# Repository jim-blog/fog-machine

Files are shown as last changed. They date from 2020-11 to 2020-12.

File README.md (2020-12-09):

# Fog Machine Control
*Control a fog machine with Arduino UNO and NW.js React app.*

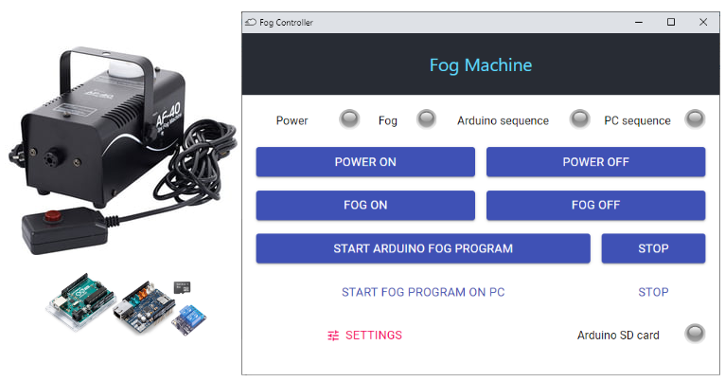
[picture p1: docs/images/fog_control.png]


## Overview

The Fog Machine is one of the most popular props in Escape Rooms, offering spooky supernatural effects or revealing light or laser beams.

## What we need

* basic fog machine with a ***wired*** remote control
* Arduino UNO with Ethernet shield and SD card
* SRD relay shield

 120/220V **10A** relays are required because fog machine power is 400W - 700W or more.</src>

## Hacking the fog machine
It is as simple as cutting and rewiring the power cable and the remote control cable.

> Open the wired remote control box and replace the pushbutton connection with a connection to the SRD relay shield.

This video may help: 
* <a href="https://www.youtube.com/watch?v=Y6d89PBlxrk" target="_blank">Controlling a Fog Machine with a Prop Controller or Relay</a>

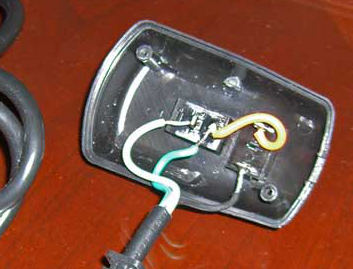
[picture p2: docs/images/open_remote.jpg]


## Wiring the Arduino prop and the fog machine
The SD card is necessary to store the fog sequence but optional if you want to control the fog sequence from the controller app only:
> Fog sequence: spit fog for *T2* seconds, pause *T3* seconds, do that *N* times then pause *T1* minutes and starts again for ever.

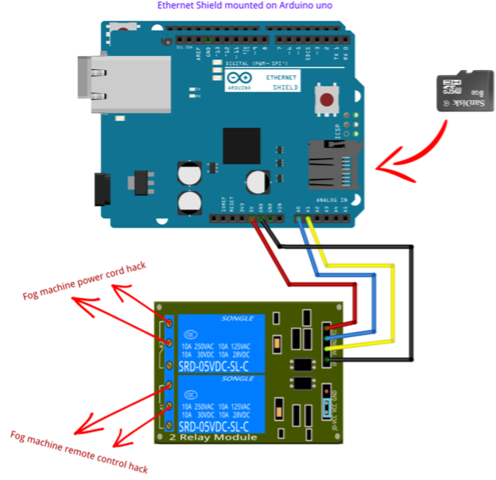
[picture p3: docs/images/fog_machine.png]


## Edit and upload the Arduino sketch

Install lastest <a href="https://www.arduino.cc/en/software" target="_blank">Arduino IDE</a> and download the <a href="https://github.com/jim-blog/fog-machine/raw/master/arduino/FogMachine.zip" target="_blank">FogMachine sketch</a> available from <a href="https://github.com/jim-blog/fog-machine/tree/master/arduino" target="_blank">this GitHub repository</a>.

Open **FogMachine** sketch in Arduino IDE and set the Arduino IP address:

```cpp
String ip = "192.168.1.201"; //<<< ENTER YOUR IP ADDRESS HERE
```

Upload **FogMachine** sketch to the Arduino

```dos
Sketch uses 27460 bytes (85%) of program storage space. Maximum is 32256 bytes.
Global variables use 1127 bytes (55%) of dynamic memory, leaving 921 bytes for local variables. Maximum is 2048 bytes.

```

## Install Fog Controller app for Windows

Download and unzip the app archive:
* <a href="https://github.com/jim-blog/fog-machine/raw/master/bin/win64/fog-controller-win64.zip">fog-controller-win64.zip</a> (92.1 MB)

Alternatively, download the `.7z` app archive and unzip with <a href="https://www.7-zip.org/" target="_blank">7-Zip</a>:
* <a href="https://github.com/jim-blog/fog-machine/raw/master/bin/win64/fog-controller-win64.7z">fog-controller-win64.7z</a> (64.6 MB)

Run `fog-controller.exe`
> If necessary, pass protection *Windows Smartscreen* that prevents the execution of the downloaded file.

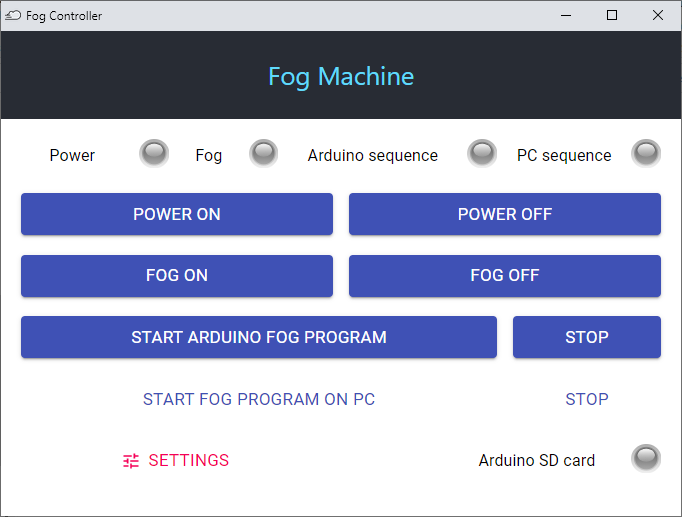
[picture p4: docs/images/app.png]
App


<a href="https://github.com/jim-blog/fog-machine/tree/master/src" target="_blank">Fog Controller app source code</a> is available from this GitHub repository, as a Javascript coder, feel free to fork and hack your own controller app.

## Set the Fog program sequence
Fog program sequence: 
* spit fog for *T2* seconds, pause *T3* seconds, do that *N* times then pause *T1* minutes and starts again for ever.

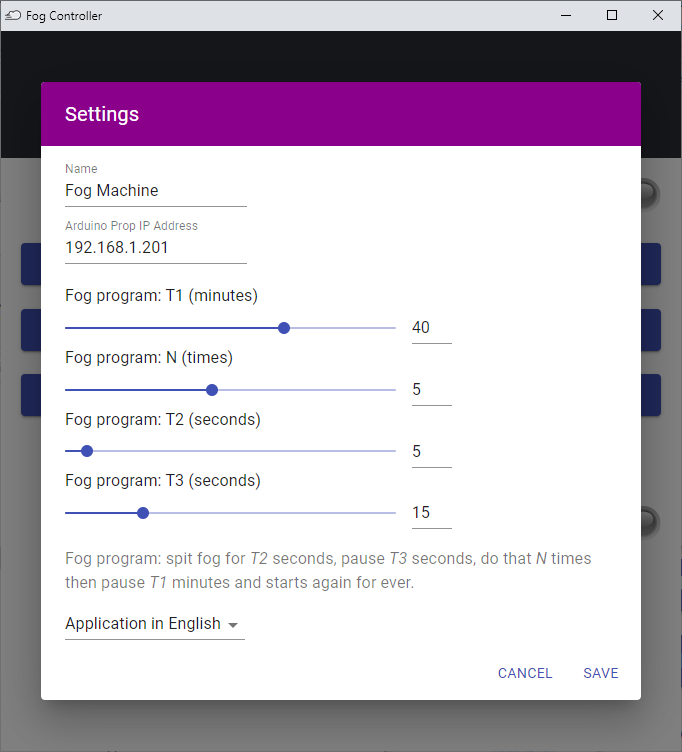
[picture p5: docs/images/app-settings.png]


## Fog prop in Escape Room

### <a href="https://houdinimc.com/" target="_blank">Houdini MC</a> users

<a href="https://houdinimc.com/" target="_blank">Houdini MC</a> control props with HTTP GET/POST requests (see <a href="https://houdinimc.com/2018/04/13/interact-with-a-controller/" target="_blank">Interacting with a Controller (e.g. Arduino/Raspberry Pi) tutorial</a>).

#### Arduino FogMachine API:

| API | RESPONSE | DESCRIPTION |
|---|---|---|
| GET /fog/1 | 200 - OK | Activate fog relay |
| GET /fog/0 | 200 - OK | Deactivate fog relay |
| GET /power/1 | 200 - OK | Activate power relay |
| GET /power/0 | 200 - OK | Deactivate power relay |
| GET /sequence/1 | 200 - OK | Start fog program sequence |
| GET /sequence/0 | 200 - OK | Stop fog program sequence |
| GET /settings/37,3,5,15  | 200 - OK | Set T1,N,T2,T3 |
| GET / | 37&#124;3&#124;5&#124;15&#124;0&#124;0&#124;0&#124;0 | T1&#124;N&#124;T2&#124;T3&#124;power&#124;fog&#124;sequence&#124;sd card |

### <a href="https://xcape.io/room/" target="_blank">xcape.io Room</a> users

<a href="https://xcape.io/room/" target="_blank">xcape.io Room</a> software use MQTT and offers automation to control finely Fog Machines.

<a href="https://xcape.io/room/" target="_blank">xcape.io</a> provides source code for many props at GitHub:
* <a href="https://github.com/xcape-io/RelayProp" target="_blank">Relay Prop</a>: a no-code prop and control panel to command relays with Arduino Mega 2560
* <a href="https://github.com/xcape-io/ArduinoProps" target="_blank">ArduinoProps library</a> and its examples
* <a href="https://github.com/xcape-io/PyPropControl" target="_blank">PyQt5 Prop Control library</a>: PyQt5 library to create control panels for escape room props

> With <a href="https://xcape.io/public/documentation/en/room/Configureautomaticevents.html" target="_blank">xcape.io Room automation</a>, the fog machine can be fully controlled, including 3-5 minutes preheating.  

## What next ?
You'll find here all the source code to hack and build your own Fog Controller app or Arduino FogMachine sketch:
* app is available in English and French, you can easily add your own language
* you can replace the Arduino Ethernet Shield with Arduino Nano, Arduino MKR Wifi 1010 or any other Arduino compatible board
* all the source code is available in this repository with some documentation:
    - <a href="https://github.com/jim-blog/fog-machine/tree/master/docs/developer/electronics" target="_blank">Electronics with `fog_machine.fzz` Fritzing project</a>
    - <a href="https://github.com/jim-blog/fog-machine/tree/master/docs/developer/arduino" target="_blank">Arduino developer notes</a>
    - <a href="https://github.com/jim-blog/fog-machine/tree/master/docs/developer/app" target="_blank">NW.js React developer notes</a>

## Author

**Jean-Michel _(Jim)_ FAURE** (December 8th, 2020)
* company: FAURE SYSTEMS®
* mail: *dev at faure dot systems*
* github: <a href="https://github.com/fauresystems" target="_blank">fauresystems</a>
* web: <a href="https://faure.systems/" target="_blank">Faure●Systems</a>

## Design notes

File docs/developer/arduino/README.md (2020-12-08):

# Arduino developer notes
*Tips and what I learnt during this project.*

## Why not use JSON on Arduino Uno ?
It's always good to use JSON in machine-to-machine communications, especially for IoT.

However, most JSON implementations, even for MCU, use nested calls which can end in a stack overflow and the Arduino Uno simply and ***silently*** crashes (which is difficult to find and fix in production).

### ArduinoJson resources
* <a href="https://arduinojson.org/" target="_blank">ArduinoJson library</a>
* <a href="https://arduinojson.org/v6/how-to/reuse-a-json-document/" target="_blank">The best way to use ArduinoJson</a>

## Restrict the API server at the very minimum on Arduino Uno
Arduino Uno has not enough memory for:
* parsing and bulding JSON objects
* handling web services nicely with several HTTP response codes (200, 400, 403, 404, 405, 408)

Limit HTTP respone code to:
* 200 OK
* 404 Not Found

## SD Card Module with Arduino
* <a href="https://github.com/greiman/SdFat" target="_blank">SdFat Version 2</a>
* <a href="https://randomnerdtutorials.com/guide-to-sd-card-module-with-arduino/" target="_blank">Guide to SD Card Module with Arduino</a>

| **SD card module** | **Wiring to Arduino Uno** | **Wiring to Arduino Mega** |
| --- | --- | --- |
| VCC | 3.3V or 5V (check module’s datasheet) | 3.3V or 5V (check module’s datasheet) |
| CS | 4 | 53 |
| MOSI | 11 | 51 |
| CLK | 13 | 52 |
| MISO | 12 | 50 |
| GND | GND | GND |

## *SdFat* library is required for long file names

#### We dont need *SdFat* library, *SD* library is good enough

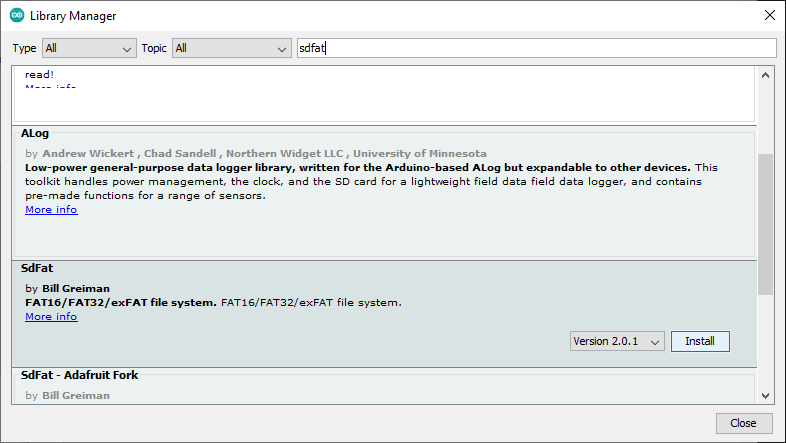
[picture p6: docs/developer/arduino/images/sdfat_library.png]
Install SdFat library


If you're new with Arduino IDE:

* <a href="https://www.arduino.cc/en/Guide/Libraries" target="_blank">Getting Started > Installing Additional Arduino Libraries</a>
* <a href="https://www.digikey.com/en/maker/blogs/2018/how-to-install-arduino-libraries" target="_blank">How to Install Arduino Libraries</a>

## Author
**Jean-Michel _(Jim)_ FAURE** (December 3rd, 2020)
* company: FAURE SYSTEMS®
* mail: *ai at faure dot systems*
* github: <a href="https://github.com/fauresystems" target="_blank">fauresystems</a>
* web: <a href="https://faure.systems/" target="_blank">Faure●Systems</a>

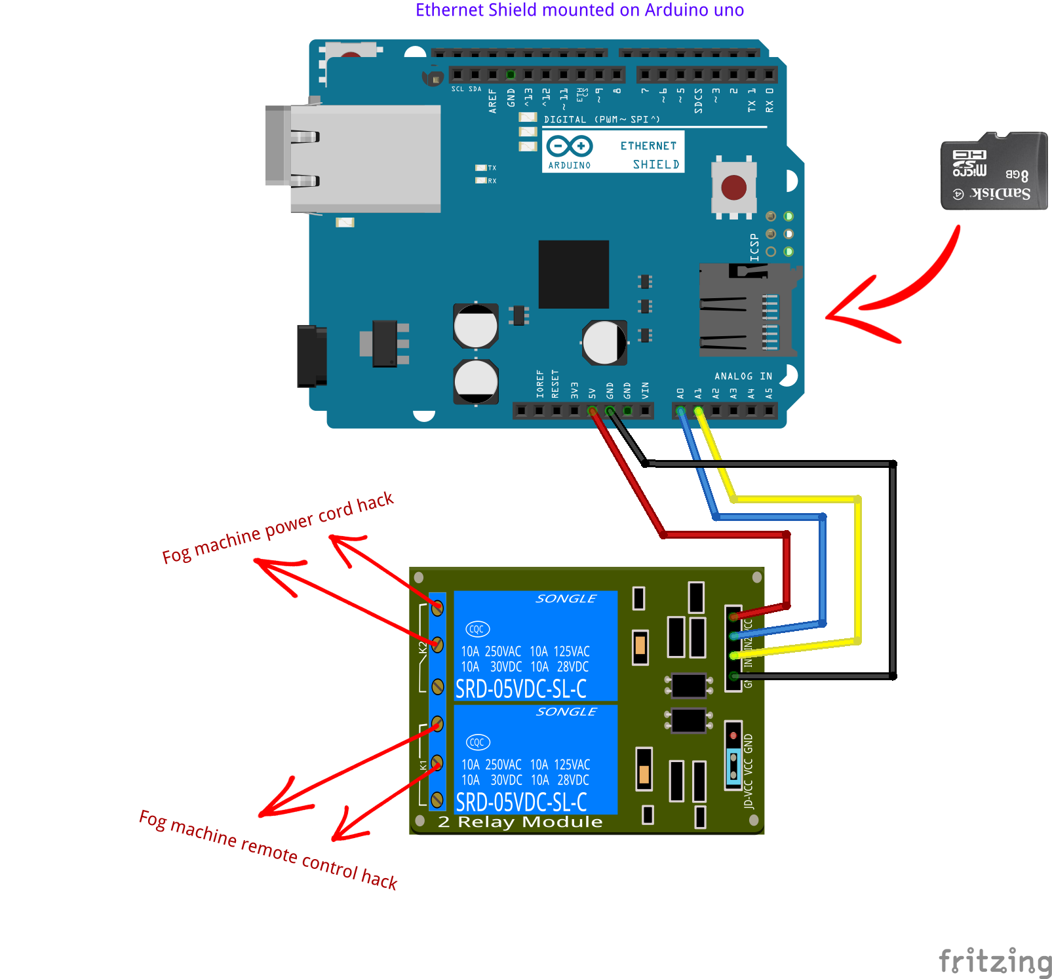
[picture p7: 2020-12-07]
docs/developer/electronics/fog_machine_bb.png

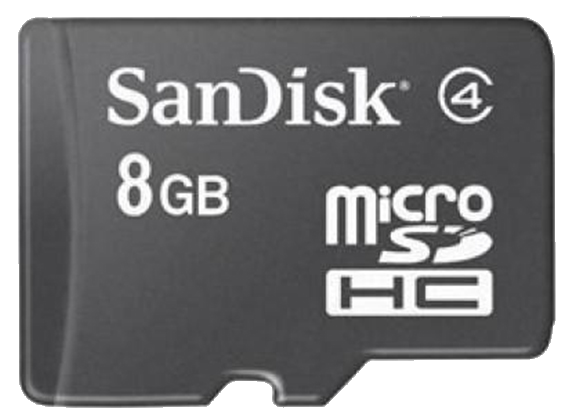
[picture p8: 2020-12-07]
docs/developer/electronics/fritzing_assets/micro-sd.png

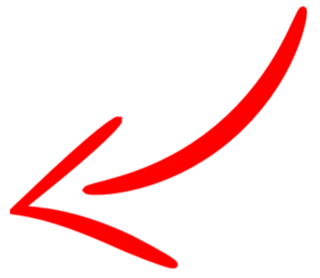
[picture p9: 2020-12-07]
docs/developer/electronics/fritzing_assets/down-to-left-arrow.png

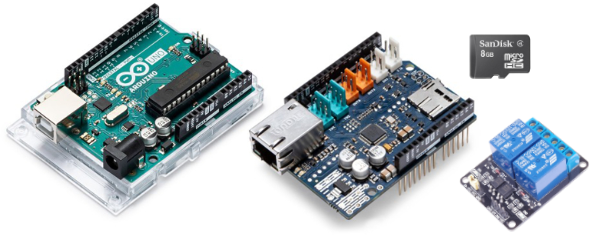
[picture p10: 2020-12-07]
docs/developer/arduino/images/hardware.png

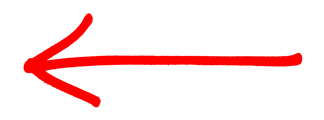
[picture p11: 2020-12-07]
docs/developer/electronics/fritzing_assets/left-arrow.png

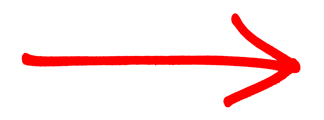
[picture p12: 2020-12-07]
docs/developer/electronics/fritzing_assets/right-arrow.png

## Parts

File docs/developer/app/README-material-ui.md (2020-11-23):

# Material UI
*Add Mateial-UI to NW.js React app.*

## Installing Material-UI Library & Dependencies

```bash
$ npm install @material-ui/core
$ npm install contentful
```

## More modules
 
```bash
$ npm install @material-ui/icons
```

## Resources

* <a href="https://medium.com/codingthesmartway-com-blog/getting-started-with-material-ui-for-react-material-design-for-react-364b2688b555" target="_blank">Getting Started With Material-UI For React (Material Design For React)</a>
* <a href="https://material-ui.com/components/material-icons/" target="_blank">Material Icons</a>

## Author

**Jean-Michel _(Jim)_ FAURE** (November 20th, 2020)
* company: FAURE SYSTEMS®
* mail: *dev at faure dot systems*
* github: <a href="https://github.com/fauresystems" target="_blank">fauresystems</a>
* web: <a href="https://faure.systems/" target="_blank">Faure●Systems</a>

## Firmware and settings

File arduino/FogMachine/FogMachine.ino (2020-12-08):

/* FogMachine.ino
   MIT License (c) Faure Systems <dev at faure dot systems>

   SD card module   Arduino Uno     Arduino Mega
      VCC             3.3V or 5V      3.3V or 5V (check module’s datasheet)
      CS              4               53
      MOSI            11              51
      CLK             13              52
      MISO            12              50
      GND             GND             GND
*/

#include <SPI.h>
#include <SD.h>
#include <Ethernet.h>
#include <IPAddress.h>
#include "lib.h"

String ip = "192.168.1.201"; //<<< ENTER YOUR IP ADDRESS HERE

const uint8_t SD_CS_PIN = 4;    // SD card chip select pin

const uint8_t PIN_POWER = A0;
const uint8_t PIN_FOG = A1;

EthernetServer server(80);       // create a server at port 80

struct state_t state = {
  0,
  { 10, 3, 5, 15 },
  { 0, 0, 0}
};

Sequence sequence(PIN_FOG);

String recv_str;
byte mac[6];

void setup()
{
  Serial.begin(9600); // for debugging

  IPAddress ipa;
  if (ipa.fromString(ip)) {
    safe_mac(mac, ip.substring(ip.lastIndexOf('.') + 1).toInt());
    Ethernet.begin(mac, ipa);
  } else {
    Serial.print(F("Invalid IP address: "));
    Serial.println(ip);
    while (true) {
      delay(1); // do nothing, no point running without valid IP address
    }
  }

  // Check for Ethernet hardware present
  if (
    Ethernet.hardwareStatus() == EthernetNoHardware) {
    Serial.println(F("Ethernet shield was not found.  Sorry, can't run without hardware. :("));
    while (true) {
      delay(1); // do nothing, no point running without Ethernet hardware
    }
  }

  Serial.print(F("IP address: "));
  Serial.println(Ethernet.localIP());

  Serial.print(F("Initializing SD card..."));
  delay(1500);

  if (SD.begin(SD_CS_PIN)) {
    Serial.println(F("initialization done."));
    state.sd = 1;
  } else {
    Serial.println(F("initialization failed!"));
  }

  if (state.sd == 1) {
    if (SD.exists(F("SETTINGS.CFG"))) {
      File fp = SD.open(F("SETTINGS.CFG"));
      if (fp) {
        String str;
        while (fp.available()) {
          char c = fp.read();
          str += c;
        }
        fp.close();
        setSettings(str);
        Serial.print(F("Settings loaded from SD card: "));
        Serial.println(str);
      } else {
        Serial.println(F("Failed to open SETTINGS.CFG for reading."));
      }
    } else {
      Serial.println(F("Configuration file SETTINGS.CFG not found."));
    }
  }

  server.begin();           // start to listen for clients

  pinMode(PIN_POWER, OUTPUT);
  pinMode(PIN_FOG, OUTPUT);

  digitalWrite(PIN_POWER, state.machine.power);
  digitalWrite(PIN_FOG, state.machine.fog);

  sequence.configure(&state.settings);
}

void loop()
{
  // Listen controller: reply state or do stuff
  EthernetClient client = server.available();  // try to get client

  if (client) {
    ////Serial.println("--new client");
    // an http request ends with a blank line
    boolean currentLineIsBlank = true;
    recv_str = "";
    while (client.connected()) {
      if (client.available()) {
        char c = client.read();
        recv_str += c;
        ////Serial.write(c);
        // if you've gotten to the end of the line (received a newline
        // character) and the line is blank, the http request has ended,
        // so you can send a reply
        if (c == '\n' && currentLineIsBlank) {
          if (recv_str.startsWith(F("GET / "))) {
            ////Serial.println(F("200 - OK"));
            writeResponse(client, 200, &String(stateResponse()));
          } else if (recv_str.startsWith(F("GET /fog/"))) {
            if (recv_str.startsWith(F("GET /fog/1"))) {
              state.machine.fog = 1;
            } else { // GET /machine/fog/0
              state.machine.fog = 0;
            }
            digitalWrite(PIN_FOG, state.machine.fog);
            Serial.println(F("200 - OK"));
            writeResponse(client, 200, &String(stateResponse()));
          } else if (recv_str.startsWith(F("GET /power/"))) {
            if (recv_str.startsWith(F("GET /power/1 "))) {
              state.machine.power = 1;
            } else { // GET /machine/power/
              state.machine.power = 0;
            }
            digitalWrite(PIN_POWER, state.machine.power);
            Serial.println(F("200 - OK"));
            writeResponse(client, 200, &String(stateResponse()));
          } else if (recv_str.startsWith(F("GET /sequence/"))) {
            if (recv_str.startsWith(F("GET /sequence/1 "))) {
              state.machine.sequence = 1;
              sequence.start();
            } else { // GET /machine/sequence/
              if (state.machine.sequence == 1) {
                state.machine.sequence = 0;
                digitalWrite(PIN_FOG, LOW);
                sequence.stop();
              }
            }
            Serial.println(F("200 - OK"));
            writeResponse(client, 200, &String(stateResponse()));
          } else if (recv_str.startsWith(F("GET /settings/"))) {
            int data_end = recv_str.indexOf(' ', 14);
            if (data_end > 14) {
              setSettings(recv_str.substring(14, data_end));
              if (SD.exists(F("SETTINGS.CFG"))) {
                SD.remove(F("SETTINGS.CFG"));
              }
              File fp = SD.open(F("SETTINGS.CFG"), FILE_WRITE);
              if (fp) {
                fp.println(recv_str.substring(14, data_end));
                fp.close();
                Serial.print(F("Settings saved to SD card:"));
                Serial.println(recv_str.substring(14, data_end));
              } else {
                Serial.println(F("Failed to open SETTINGS.CFG for writing."));
              }
            }
            Serial.println(F("200 - OK"));
            writeResponse(client, 200, &String(stateResponse()));
          } else {
            Serial.println(F("404 - NOT FOUND"));
            writeResponse(client, 404);
          }
          break;
        }
        if (c == '\n') {
          // you're starting a new line
          currentLineIsBlank = true;
        } else if (c != '\r') {
          // you've gotten a character on the current line
          currentLineIsBlank = false;
        }
      }
    }
    // give the web browser time to receive the data
    delay(1);
    // close the connection:
    client.stop();
    ////Serial.println("--client disconnected");
  } // end if (client)

  sequence.update();
}

void readState() {
  state.machine.power = digitalRead(PIN_POWER);
  state.machine.fog = digitalRead(PIN_FOG);
}

String stateResponse() {
  readState();
  String str;
  str += String(state.settings.t1, DEC);
  str += '|';
  str += String(state.settings.n, DEC);
  str += '|';
  str += String(state.settings.t2, DEC);
  str += '|';
  str += String(state.settings.t3, DEC);
  str += '|';
  str += String(state.machine.power, DEC);
  str += '|';
  str += String(state.machine.fog, DEC);
  str += '|';
  str += String(state.machine.sequence, DEC);
  str += '|';
  str += String(state.sd, DEC);
  return str;
}

void setSettings(String str) {
  int u = 0;
  int v = str.indexOf(',');
  if (v > u) {
    state.settings.t1 = str.substring(u, v).toInt();
  }
  u = v + 1;
  v = str.indexOf(',', u);
  if (v > u) {
    state.settings.n = str.substring(u, v).toInt();
  }
  u = v + 1;
  v = str.indexOf(',', u);
  if (v > u) {
    state.settings.t2 = str.substring(u, v).toInt();
  }
  u = v + 1;
  if (u < str.length()) {
    state.settings.t3 = str.substring(u).toInt();
  }
  sequence.configure(&state.settings);
}

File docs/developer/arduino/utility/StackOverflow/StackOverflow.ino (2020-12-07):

/* StackOverflow.ino
   MIT License (c) Faure Systems <dev at faure dot systems>
*/

#include "FreeStack.h"

void setup()
{
  Serial.begin(9600);       // for debugging

  Serial.print(F("FreeStack (max for Uno: 2048, with Serial: 1853): "));
  Serial.println(FreeStack());

  unsigned long n = 40;
  Serial.println(String("Call factorial(n) with n=") + String(n, DEC));
  unsigned long y = factorial(n);
  Serial.println(String(n, DEC) + "! = " + String(y, DEC));
}

void loop()
{
  Serial.println("-- loop");
  delay(1000);
  unsigned long n = 5;
  Serial.println(String("Call factorial(n) with n=") + String(n, DEC));
  unsigned long y = factorial(n);
  Serial.println(String(n, DEC) + "! = " + String(y, DEC));
}

unsigned long factorial(unsigned long n) {
  String buf = "Store something on stack";
  String str;
  for (int i = 0; i < buf.length(); i++) {
    str[i] = buf[i];
  }
  Serial.print(F("FreeStack (max for Uno: 2048, with Serial: 1853): "));
  Serial.println(FreeStack());
  if (n == 0) return 1;
  return n * factorial(n - 1);
}

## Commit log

2020-11-23 PropButton with Material Ui Button
2020-11-23 Add Tune floating button
2020-11-26 Complete InputSlider props
2020-11-26 Add leds to panel
2020-11-26 Add leds
2020-11-30 Get Arduino state with axios
2020-11-30 Fix getArduinoState timer
2020-12-02 Give up JSON for Arduino
2020-12-03 Add fog program buttons
2020-12-05 Add led for Arduino sequence
2020-12-06 Add SD card Led
2020-12-06 Prevent Arduino sequence already running
2020-12-07 Add arduino folder
    [fog_machine.fzz]
2020-12-08 Update and rearrange documentation
    [fog_machine.fzz]
2020-12-08 Rearrange documentation
    [fog_machine.fzz]
